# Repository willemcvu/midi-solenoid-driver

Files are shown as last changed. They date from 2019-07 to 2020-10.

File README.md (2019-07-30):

# midi-solenoid-driver
A set of PCBs to drive solenoids using MIDI data, for use in automating musical instruments.

**The boards in this repo will be available for sale shortly on Tindie and/or eBay. If you are interested in buying assembled PCBs or bare PCBs, please send me a message as it would be helpful to know how many might sell. Thanks!**

The system consists of two parts: the solenoid driver board(s), and the USB interface board. The solenoid driver board(s) are daisy-chained via RJ12 ("phone cables"), and at the end of the chain is the USB interface board, which passes MIDI data from the USB port to all the solenoid driver boards (as many driver boards as are needed):

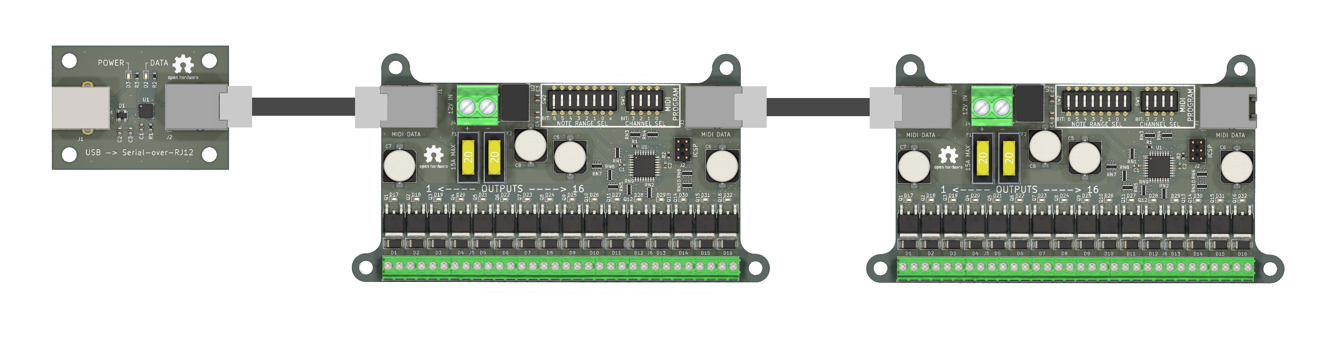
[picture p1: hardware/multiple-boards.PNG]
all boards


In addition to supporting daisy-chaining, the solenoid driver board has several notable features that allow for high usability with limited electronics experience.

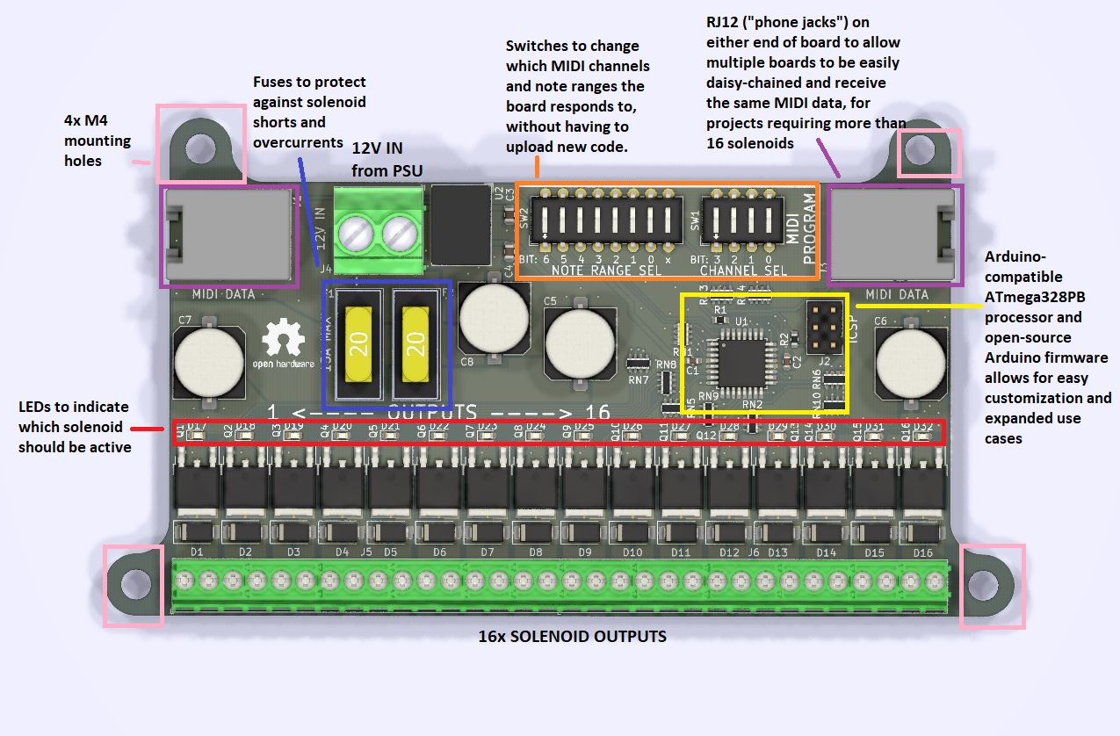
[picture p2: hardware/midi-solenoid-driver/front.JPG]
solenoid board annotated


Currently, MIDI data is fed to the solenoid drivers by a custom USB to serial-over-RJ12 board:

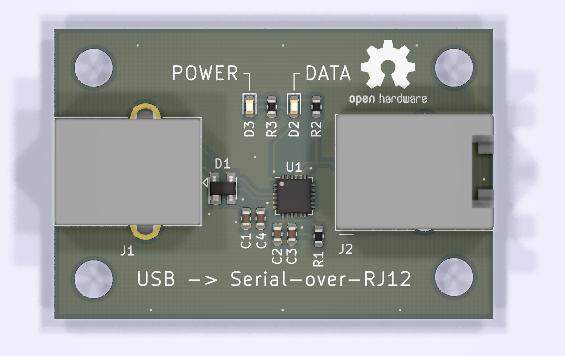
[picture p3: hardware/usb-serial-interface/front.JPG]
usb interface board


In the near future, more RJ12-compatible MIDI interface boards will be designed and released, allowing for more connectivity options. These will likely include:
 - Native plug-and-play USB MIDI (as opposed to the MIDI-over-serial in use right now)
 - Actual MIDI connector
 - Bluetooth adapter
 - AppleMIDI (RTP-MIDI / MIDI-over-network) WiFi interface

Additionally, more driver boards for devices other than solenoids will be designed/released, including a MIDI servo driver.

If you have specific needs for a particular project and need customized hardware, I can probably accomodate. Open an issue or contact me via my blog (https://willemhillier.wordpress.com/)and we'll go from there.

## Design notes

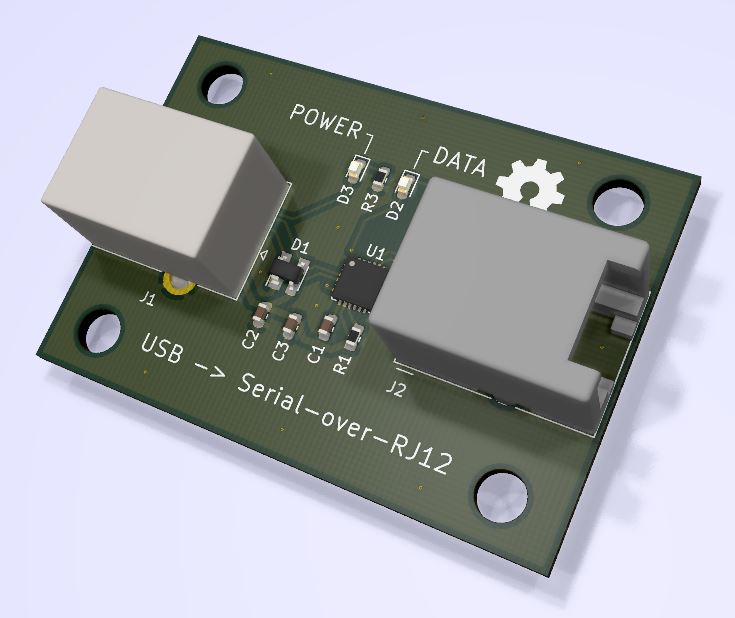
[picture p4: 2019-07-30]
hardware/usb-serial-interface/3d.JPG

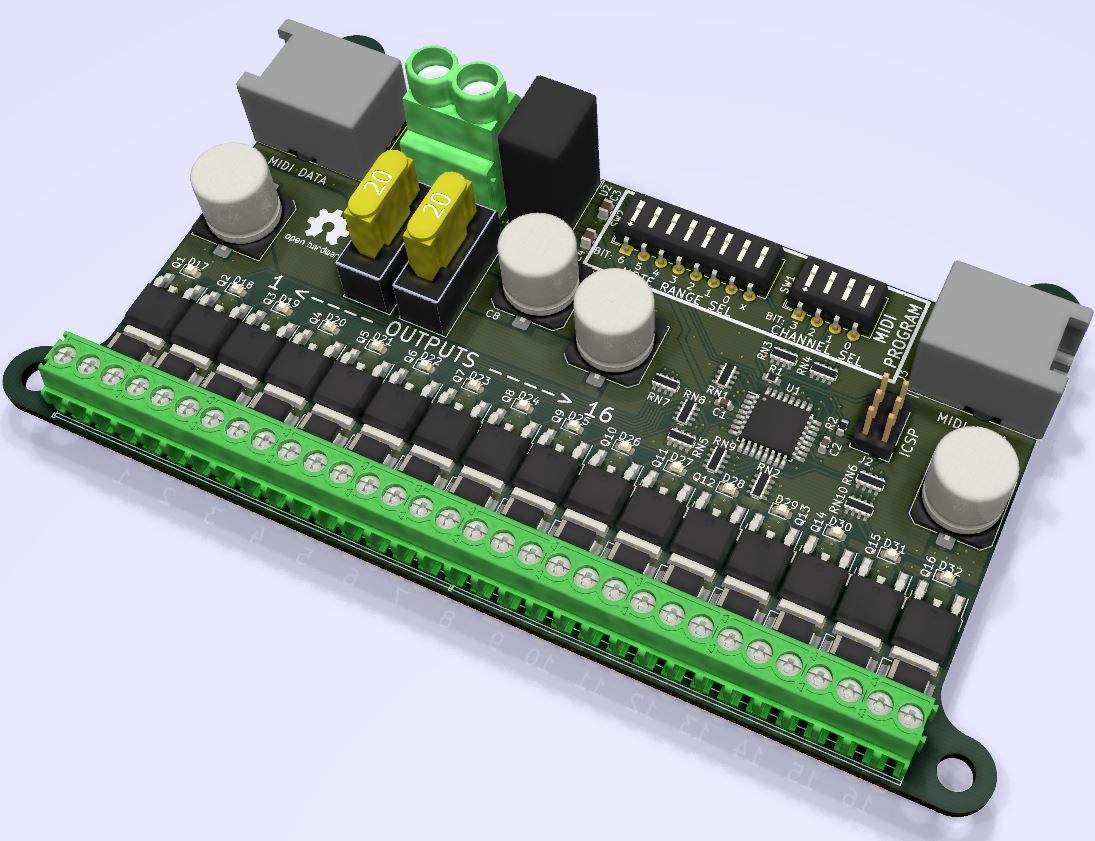
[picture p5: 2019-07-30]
hardware/midi-solenoid-driver/3d.JPG

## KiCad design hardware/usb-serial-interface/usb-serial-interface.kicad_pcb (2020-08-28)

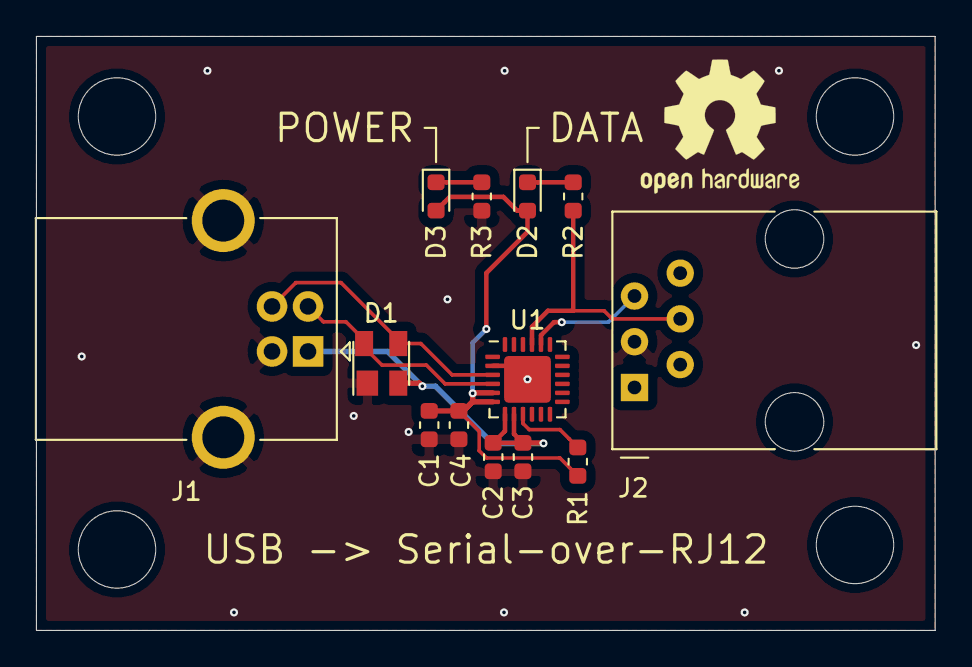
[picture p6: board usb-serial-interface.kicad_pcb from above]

Board: 2 copper layers, 49.9 x 33.0 mm, 13 parts (0 on the bottom side), 10 nets.

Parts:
C1, C2: 4.7u; C_0603_1608Metric
C3, C4: 0.1u; C_0603_1608Metric
D1: SP0503BAHT; SOT-143
D2, D3: LED; LED_0603_1608Metric
J1: USB_B; USB_B_OST_USB-B1HSxx_Horizontal
J2: RJ12; RJ12_Amphenol_54601
R1: 4.7k; R_0603_1608Metric
R2, R3: 1k; R_0603_1608Metric
U1: CP2102N-A01-GQFN24; QFN-24-1EP_4x4mm_P0.5mm_EP2.6x2.6mm

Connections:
+3V3: C1.1, C4.1, D2.2, D3.2, R1.1, U1.5, U1.6
/D+: D1.3, J1.3, U1.3
/D-: D1.4, J1.2, U1.4
/RXD: J2.5, U1.20
/TXD: J2.4, R2.1, U1.21
GND: C1.2, C2.2, C3.2, C4.2, D1.1, J1.4, J1.5, J2.3, R3.1, U1.2, U1.25
unnamed: D2.1, R2.2
unnamed: D3.1, R3.2
unnamed: R1.2, U1.9
VBUS: C2.1, C3.1, D1.2, J1.1, U1.7, U1.8

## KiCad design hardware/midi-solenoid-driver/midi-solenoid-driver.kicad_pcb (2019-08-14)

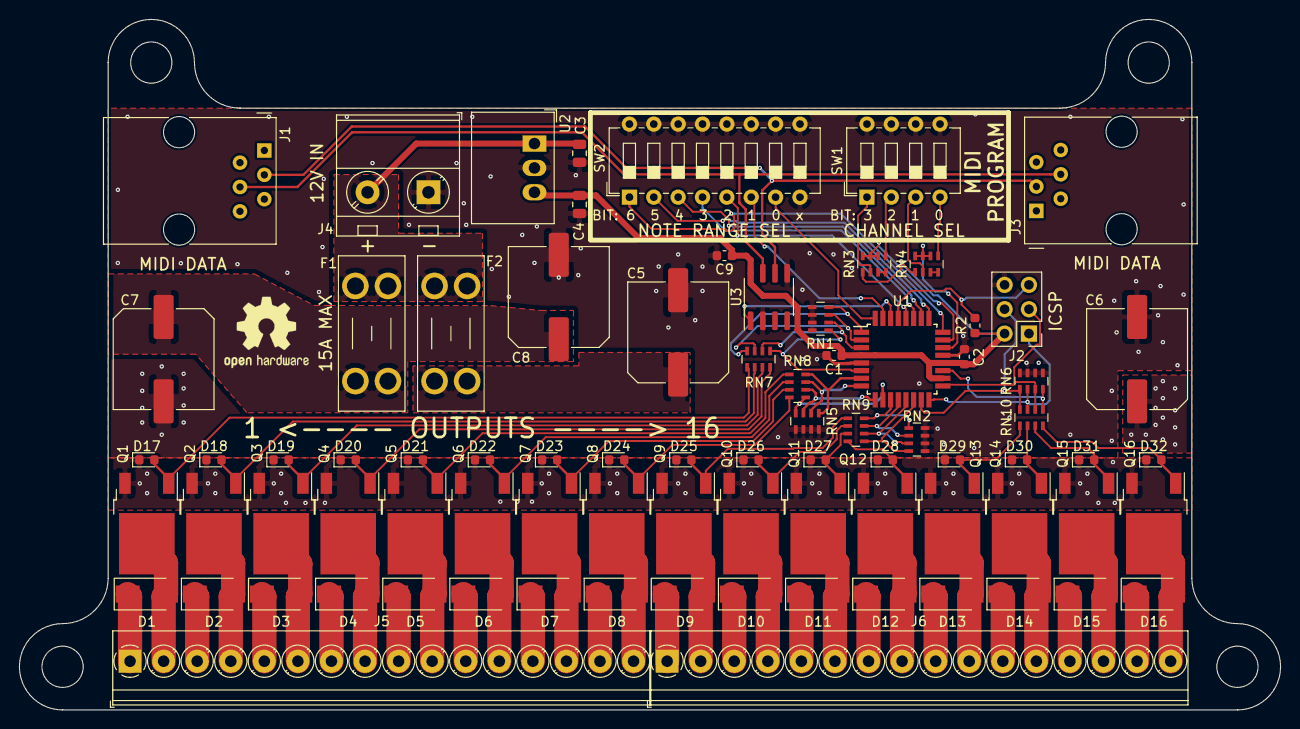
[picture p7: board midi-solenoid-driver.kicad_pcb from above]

Board: 2 copper layers, 131.5 x 72.0 mm, 81 parts (0 on the bottom side), 72 nets.

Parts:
C1, C2, C9: 0.1uF; C_0603_1608Metric
C3, C4: 10uF; C_0805_2012Metric
C5, C6, C7, C8: 470; C_Elec_10x10.2
D1, D2, D3, D4, D5, D6, D7, D8, D9, D10, D11, D12, D13, D14, D15, D16: D_Small; D_SMA
D17, D18, D19, D20, D21, D22, D23, D24, D25, D26, D27, D28, D29, D30, D31, D32: LED_Small; LED_0603_1608Metric
F1, F2: 20A; Fuseholder_Blade_Mini_Keystone_3568
J1: LEFT_DATA; RJ12_Amphenol_54601
J2: Conn_02x03_Odd_Even; PinHeader_2x03_P2.54mm_Vertical
J3: RIGHT_DATA; RJ12_Amphenol_54601
J4: 12V_IN; TerminalBlock_MetzConnect_Type701_RT11L02HGLU_1x02_P6.35mm_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
J5: SOLENOIDS_OUT_1; TerminalBlock_Phoenix_PT-1,5-16-3.5-H_1x16_P3.50mm_Horizont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
J6: SOLENOIDS_OUT_2; TerminalBlock_Phoenix_PT-1,5-16-3.5-H_1x16_P3.50mm_Horizont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
Q1, Q2, Q3, Q4, Q5, Q6, Q7, Q8, Q9, Q10, Q11, Q12, Q13, Q14, Q15, Q16: Q_NMOS_GDS; TO-252-2
R2: 10k; R_0603_1608Metric
RN1, RN2, RN3, RN4, RN5, RN6: 10k; R_Array_Concave_4x0603
RN7, RN8, RN9, RN10: 1k; R_Array_Concave_4x0603
SW1: MIDI_CHANNEl; SW_DIP_SPSTx04_Slide_6.7x11.72mm_W7.62mm_P2.54mm_LowProfile
SW2: SW_DIP_x08; SW_DIP_SPSTx08_Slide_6.7x21.88mm_W7.62mm_P2.54mm_LowProfile
U1: ATmega328PB-AU; TQFP-32_7x7mm_P0.8mm
U2: R-78B5.0-2.0; Converter_DCDC_RECOM_R-78B-2.0_THT
U3: SN75LBC176D; SOIC-8_3.9x4.9mm_P1.27mm

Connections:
+5V: C1.1, C2.1, C4.1, C9.1, J2.2, R2.1, RN3.1, RN4.1, U1.4, U1.18, U1.20, U2.3, U3.8
+12V: C3.1, F1.2, F2.2, J4.2, U2.1
/12V_FUSED1: C7.1, C8.1, D1.1, D2.1, D3.1, D4.1, D5.1, D6.1, D7.1, D8.1, F1.1, J5.1, J5.3, J5.5, J5.7, J5.9, J5.11, J5.13, J5.15
/12V_FUSED2: C5.1, C6.1, D9.1, D10.1, D11.1, D12.1, D13.1, D14.1, D15.1, D16.1, F2.1, J6.1, J6.3, J6.5, J6.7, J6.9, J6.11, J6.13, J6.15
/CTRL1: RN1.4, RN7.8, U1.1
/CTRL2: RN1.3, RN7.7, U1.2
/CTRL3: RN1.2, RN7.6, U1.3
/CTRL4: RN1.1, RN7.5, U1.6
/CTRL5: RN5.1, RN8.8, U1.7
/CTRL6: RN5.2, RN8.7, U1.8
/CTRL7: RN5.3, RN8.6, U1.9
/CTRL8: RN5.4, RN8.5, U1.10
/CTRL9: RN2.1, RN9.8, U1.11
/CTRL10: RN2.2, RN9.7, U1.12
/CTRL11: RN2.3, RN9.6, U1.13
/CTRL12: RN2.4, RN9.5, U1.14
/CTRL13: J2.4, RN6.1, RN10.8, U1.15
/CTRL14: J2.1, RN6.2, RN10.7, U1.16
/CTRL15: J2.3, RN6.3, RN10.6, U1.17
/CTRL16: RN6.4, RN10.5, U1.19
/GATE1: D17.2, Q1.1, RN7.1
/GATE2: D18.2, Q2.1, RN7.2
/GATE3: D19.2, Q3.1, RN7.3
/GATE4: D20.2, Q4.1, RN7.4
/GATE5: D21.2, Q5.1, RN8.1
/GATE6: D22.2, Q6.1, RN8.2
/GATE7: D23.2, Q7.1, RN8.3
/GATE8: D24.2, Q8.1, RN8.4
/GATE9: D25.2, Q9.1, RN9.1
/GATE10: D26.2, Q10.1, RN9.2
/GATE11: D27.2, Q11.1, RN9.3
/GATE12: D28.2, Q12.1, RN9.4
/GATE13: D29.2, Q13.1, RN10.1
/GATE14: D30.2, Q14.1, RN10.2
/GATE15: D31.2, Q15.1, RN10.3
/GATE16: D32.2, Q16.1, RN10.4
/MIDI_CH_BIT0-1: RN3.6, RN3.7, RN3.8, U1.23
/MIDI_CH_BIT2-3: RN4.6, RN4.7, RN4.8, U1.22
/MIDI_IN: U1.30, U3.1
/MIDI_NOTE_BIT0: SW2.1, U1.24
/MIDI_NOTE_BIT1: SW2.2, U1.25
/MIDI_NOTE_BIT2: SW2.3, U1.26
/MIDI_NOTE_BIT3: SW2.4, U1.27
/MIDI_NOTE_BIT4: SW2.5, U1.28
/MIDI_NOTE_BIT5: SW2.6, U1.31
/MIDI_NOTE_BIT6: SW2.7, U1.32
/OUT1: D1.2, J5.2, Q1.2
/OUT2: D2.2, J5.4, Q2.2
/OUT3: D3.2, J5.6, Q3.2
/OUT4: D4.2, J5.8, Q4.2
/OUT5: D5.2, J5.10, Q5.2
/OUT6: D6.2, J5.12, Q6.2
/OUT7: D7.2, J5.14, Q7.2
/OUT8: D8.2, J5.16, Q8.2
/OUT9: D9.2, J6.2, Q9.2
/OUT10: D10.2, J6.4, Q10.2
/OUT11: D11.2, J6.6, Q11.2
/OUT12: D12.2, J6.8, Q12.2
/OUT13: D13.2, J6.10, Q13.2
/OUT14: D14.2, J6.12, Q14.2
/OUT15: D15.2, J6.14, Q15.2
/OUT16: D16.2, J6.16, Q16.2
/RESET: J2.5, R2.2, U1.29
/RS485_A: J1.3, J3.3, U3.6
/RS485_B: J1.4, J3.4, U3.7
GND: C1.2, C2.2, C3.2, C4.2, C5.2, C6.2, C7.2, C8.2, C9.2, D17.1, D18.1, D19.1, D20.1, D21.1, D22.1, D23.1, D24.1, D25.1, D26.1, D27.1, D28.1, D29.1, D30.1, D31.1, D32.1, J2.6, J4.1, Q1.3, Q2.3, Q3.3, Q4.3, Q5.3, Q6.3, Q7.3, Q8.3, Q9.3, Q10.3, Q11.3, Q12.3, Q13.3, Q14.3, Q15.3, Q16.3, RN1.5, RN1.6, RN1.7, RN1.8, RN2.5, RN2.6, RN2.7, RN2.8, RN5.5, RN5.6, RN5.7, RN5.8, RN6.5, RN6.6, RN6.7, RN6.8, SW1.5, SW1.6, SW1.7, SW1.8, SW2.8, SW2.9, SW2.10, SW2.11, SW2.12, SW2.13, SW2.14, SW2.15, SW2.16, U1.5, U1.21, U2.2, U3.2, U3.5
unnamed: RN3.2, SW1.1
unnamed: RN3.3, RN3.4
unnamed: RN3.5, SW1.2
unnamed: RN4.2, SW1.3
unnamed: RN4.3, RN4.4
unnamed: RN4.5, SW1.4

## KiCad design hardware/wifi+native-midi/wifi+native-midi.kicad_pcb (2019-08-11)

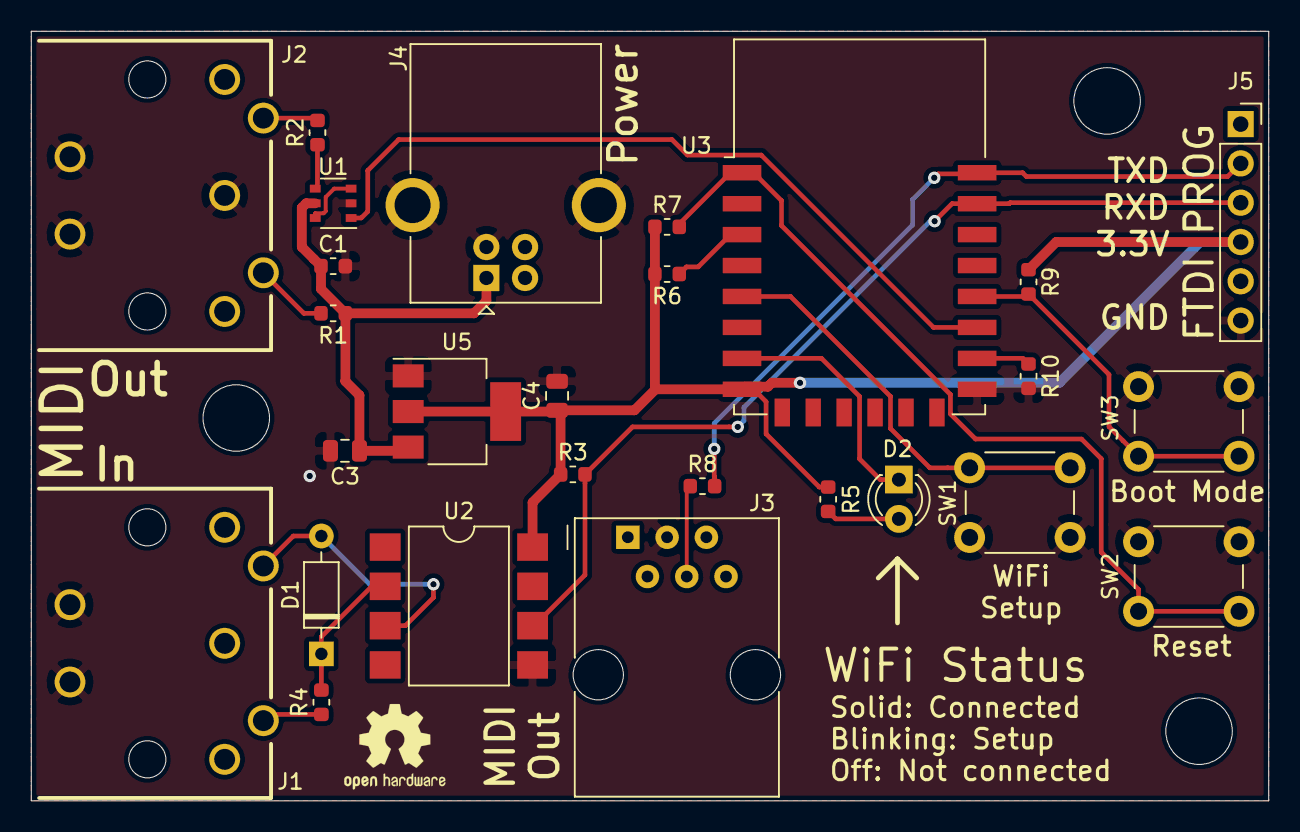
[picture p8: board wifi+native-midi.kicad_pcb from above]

Board: 2 copper layers, 80.0 x 49.8 mm, 27 parts (0 on the bottom side), 21 nets.

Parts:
C1: 0.1u; C_0603_1608Metric
C3, C4: 10u; C_0805_2012Metric
D1: 1N914; D_DO-35_SOD27_P7.62mm_Horizontal
D2: LED; LED_D3.0mm
J1: MIDI_RX; 57PC5F_5_DIN_MIDI_GENERIC
J2: MIDI_TX; 57PC5F_5_DIN_MIDI_GENERIC
J3: 6P6C; RJ12_Amphenol_54601
J4: USB_B; USB_B_OST_USB-B1HSxx_Horizontal
J5: FTDI; PinSocket_1x06_P2.54mm_Vertical
R1, R2: 220; R_0603_1608Metric
R3: 470; R_0603_1608Metric
R4, R5: 1k; R_0603_1608Metric
R6, R7, R9, R10: 10k; R_0603_1608Metric
R8: 330; R_0603_1608Metric
SW1: WIFI_CONFIG; SW_PUSH_6mm_H9.5mm
SW2: RESET; SW_PUSH_6mm_H9.5mm
SW3: BOOT_MODE; SW_PUSH_6mm_H9.5mm
U1: 74HC2G04; TSOP-6_1.65x3.05mm_P0.95mm
U2: 6N138; SMDIP-8_W9.53mm
U3: ESP-12F; ESP-12E
U5: AZ1117-3.3; SOT-223-3_TabPin2

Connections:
+3V3: C4.1, J5.4, R3.1, R5.1, R6.2, R7.1, R9.1, U2.8, U3.8, U5.2
+5V: C1.1, C3.1, J4.1, R1.1, U1.5, U5.3
/GPIO0: R9.2, SW3.2, U3.18
/MIDI_IN: J5.3, R3.2, U2.6, U3.21
/MIDI_OUT: U1.1, U3.17
/RJ12_MIDI_OUT: J5.2, R8.2, U3.22
/RST: R7.2, SW2.2, U3.1
/WIFI_CONFIG: SW1.1, U3.5
/WIFI_STATUS: D2.1, U3.7
GND: C1.2, C3.2, C4.2, J1.GND, J2.2, J2.GND, J3.3, J4.4, J4.5, J5.6, R10.2, SW1.2, SW2.1, SW3.1, U1.2, U2.5, U3.15, U5.1
unnamed: D1.1, R4.2, U2.2
unnamed: D1.2, J1.5, U2.3
unnamed: D2.2, R5.2
unnamed: J1.4, R4.1
unnamed: J2.4, R1.2
unnamed: J2.5, R2.2
unnamed: J3.4, R8.1
unnamed: R2.1, U1.4
unnamed: R6.1, U3.3
unnamed: R10.1, U3.16
unnamed: U1.3, U1.6

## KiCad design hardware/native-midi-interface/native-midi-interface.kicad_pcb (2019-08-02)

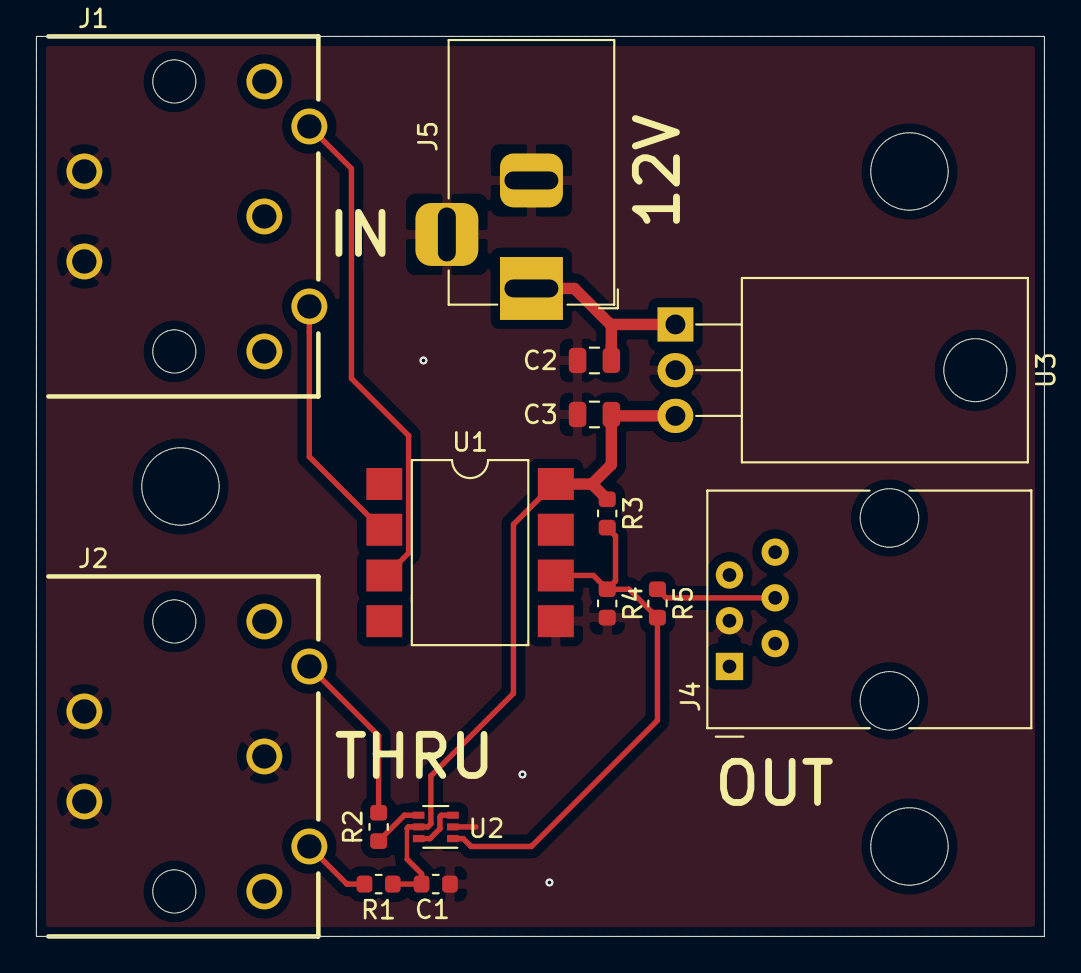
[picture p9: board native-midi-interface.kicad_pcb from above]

Board: 2 copper layers, 56.0 x 50.0 mm, 15 parts (0 on the bottom side), 11 nets.

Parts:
C1: 1u; C_0603_1608Metric
C2, C3: 10u; C_0805_2012Metric
J1: MIDI_RX; 57PC5F_5_DIN_MIDI_GENERIC
J2: MIDI_PASSTHROUGH; 57PC5F_5_DIN_MIDI_GENERIC
J4: 6P6C; RJ12_Amphenol_54601
J5: BARREL_JACK_12V; BarrelJack_Horizontal
R1, R2: 220; R_0603_1608Metric
R3: 470; R_0603_1608Metric
R4: 1k; R_0603_1608Metric
R5: 330; R_0603_1608Metric
U1: 6N138; SMDIP-8_W9.53mm
U2: 74HC2G04; SOT-363_SC-70-6
U3: L7805; TO-220-3_Horizontal_TabDown

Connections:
+5V: C1.1, C3.1, R1.1, R3.1, U1.8, U2.5, U3.3
+12V: C2.1, J5.1, U3.1
/MIDI_UART: R3.2, R4.1, R5.2, U1.6, U2.1
GND: C1.2, C2.2, C3.2, J1.GND, J2.2, J2.GND, J4.3, J5.2, J5.3, R4.2, U1.5, U2.2, U3.2
unnamed: J1.4, U1.2
unnamed: J1.5, U1.3
unnamed: J2.4, R1.2
unnamed: J2.5, R2.2
unnamed: J4.4, R5.1
unnamed: R2.1, U2.4
unnamed: U2.3, U2.6

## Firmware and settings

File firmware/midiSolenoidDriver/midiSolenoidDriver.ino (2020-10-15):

//Firmware for the MIDI solenoid driver board: https://github.com/willemcvu/midi-solenoid-driver
//Author: Willem Hillier, with MIDI decoding code taken from: https://forum.arduino.cc/index.php?topic=22447.0

//Configuration constants
#define SETUP_TEST_DELAY 100

//Pin mappings for big dip switch input, used for selecting the MIDI note number of the lowest note the board responds to
byte MIDI_NOTE_BIT[] =  {15, 16, 17, 18, 19, 1, 2};

// Digital output pin mappings in sequential order ("OUTPUTS 1-16")
byte pinNumbers[] = {3, 4, 23, 24, 20, 21, 5, 6, 7, 8, 9, 10, 11, 12, 13, 25};

// Global vars
byte MIDI_CHANNEL = 0;
byte LOWEST_MIDI_NOTE = 0;
byte incomingByte;
byte byteNumber = 0;
byte note;
byte velocity;
int action = 2;

boolean readSmallDip(int bitNo) {
  boolean bit0 = false;
  boolean bit1 = false;
  boolean bit2 = false;
  boolean bit3 = false;

  int adc_bit01_val = analogRead(A0);
  int adc_bit23_val = analogRead(A7);

  if (adc_bit01_val > 750) {
    bit0 = false;
    bit1 = false;
  } else if ((adc_bit01_val > 550) and (adc_bit01_val <= 750)) {
    bit0 = false;
    bit1 = true;
  } else if ((adc_bit01_val > 480) and (adc_bit01_val <= 550)) {
    bit0 = true;
    bit1 = false;
  } else if ((adc_bit01_val <= 480)) {
    bit0 = true;
    bit1 = true;
  }

  if (adc_bit23_val > 750) {
    bit2 = false;
    bit3 = false;
  } else if ((adc_bit23_val > 550) and (adc_bit23_val < 750)) {
    bit2 = false;
    bit3 = true;
  } else if ((adc_bit23_val > 480) and (adc_bit23_val <= 550)) {
    bit2 = true;
    bit3 = false;
  } else if ((adc_bit23_val <= 480)) {
    bit2 = true;
    bit3 = true;
  }

  if (bitNo == 0) {
    return bit0;
  } else if (bitNo == 1) {
    return bit1;
  } else if (bitNo == 2) {
    return bit2;
  } else if (bitNo == 3) {
    return bit3;
  } else {
    return false;
  }
}

void TestDipSwitches() {
  while (1 == 1) {

    //Set first 7 outputs to the state of the large dip switch
    digitalWrite(pinNumbers[0], ! digitalRead(MIDI_NOTE_BIT[6]));
    digitalWrite(pinNumbers[1], ! digitalRead(MIDI_NOTE_BIT[5]));
    digitalWrite(pinNumbers[2], ! digitalRead(MIDI_NOTE_BIT[4]));
    digitalWrite(pinNumbers[3], ! digitalRead(MIDI_NOTE_BIT[3]));
    digitalWrite(pinNumbers[4], ! digitalRead(MIDI_NOTE_BIT[2]));
    digitalWrite(pinNumbers[5], ! digitalRead(MIDI_NOTE_BIT[1]));
    digitalWrite(pinNumbers[6], ! digitalRead(MIDI_NOTE_BIT[0]));

    // Set first four outputs to the state of the small dip switch
    digitalWrite(pinNumbers[7], readSmallDip(0));
    digitalWrite(pinNumbers[8], readSmallDip(1));
    digitalWrite(pinNumbers[9], readSmallDip(2));
    digitalWrite(pinNumbers[10], readSmallDip(3));
  }
}

void setup() {
  //Set output pins mode
  for (int n = 0; n < 16; n++) {
    pinMode(pinNumbers[n], OUTPUT);
  }

  //DIP switch input mode
  for (int n = 0; n < 7; n++) {
    pinMode(MIDI_NOTE_BIT[n], INPUT_PULLUP);
  }

  // test outputs
  for (int n = 0; n < 16; n++) {
    digitalWrite(pinNumbers[n], HIGH);
    delay(SETUP_TEST_DELAY);
    digitalWrite(pinNumbers[n], LOW);
  }

  // test DIP switches
  //TestDipSwitches();
  //The above function is an infinite while-loop. Reflash this firmware with the above line uncommented, and the status of the ouputs will mirror the status of the DIP switches.
  //Useful for testing outputs and DIP switches.

  //read midi channel to respond to, zero-indexed (!! most midi software is 1-indexed !!)
  if (readSmallDip(3)) MIDI_CHANNEL = MIDI_CHANNEL + 1;
  if (readSmallDip(2)) MIDI_CHANNEL = MIDI_CHANNEL + 2;
  if (readSmallDip(1)) MIDI_CHANNEL = MIDI_CHANNEL + 4;
  if (readSmallDip(0)) MIDI_CHANNEL = MIDI_CHANNEL + 8;

  //read lowest midi note to respond to
  if (!digitalRead(MIDI_NOTE_BIT[0])) LOWEST_MIDI_NOTE = LOWEST_MIDI_NOTE + 1;
  if (!digitalRead(MIDI_NOTE_BIT[1])) LOWEST_MIDI_NOTE = LOWEST_MIDI_NOTE + 2;
  if (!digitalRead(MIDI_NOTE_BIT[2])) LOWEST_MIDI_NOTE = LOWEST_MIDI_NOTE + 4;
  if (!digitalRead(MIDI_NOTE_BIT[3])) LOWEST_MIDI_NOTE = LOWEST_MIDI_NOTE + 8;
  if (!digitalRead(MIDI_NOTE_BIT[4])) LOWEST_MIDI_NOTE = LOWEST_MIDI_NOTE + 16;
  if (!digitalRead(MIDI_NOTE_BIT[5])) LOWEST_MIDI_NOTE = LOWEST_MIDI_NOTE + 32;
  if (!digitalRead(MIDI_NOTE_BIT[6])) LOWEST_MIDI_NOTE = LOWEST_MIDI_NOTE + 64;

  //begin serial receive, no transmit
  Serial.begin(38400);
  //Disable hardware UART transmit
  UCSR0B &= ~bit (TXEN0);
}

//loop: wait for serial data, and interpret the message
void loop () {
  if (Serial.available() > 0) {
    //digitalWrite(pinNumbers[15],HIGH);
    //delay(1);
    //digitalWrite(pinNumbers[15],LOW);
    // read the incoming byte:
    incomingByte = Serial.read();

    // wait for as status-byte, channel 1, note on or off
    if (incomingByte == 144 + MIDI_CHANNEL) { // note on message starting starting
      //digitalWrite(pinNumbers[14],HIGH);
      //delay(1);
      //digitalWrite(pinNumbers[14],LOW);
      action = 1;
      byteNumber = 1;
    } else if (incomingByte == 128 + MIDI_CHANNEL) { // note off message starting
      action = 0;
      byteNumber = 1;
    } else if (incomingByte == 208) { // aftertouch message starting
      //not implemented yet
    } else if (incomingByte == 160) { // polypressure message starting
      //not implemented yet
    } else if ( (action == 0) && (byteNumber == 1) ) { // if we received a "note off", we wait for which note (databyte)
      note = incomingByte;
      playNote(note, 0);
      note = 0;
      velocity = 0;
      action = 2;
      byteNumber = 0;
    } else if ( (action == 1) && (byteNumber == 1) ) { // if we received a "note on", we wait for the note (databyte)
      note = incomingByte;
      byteNumber = 2;
    } else if ( (action == 1) && (byteNumber == 2) ) { // ...and then the velocity
      velocity = incomingByte;
      playNote(note, velocity);
      note = 0;
      velocity = 0;
      action = 0;
      byteNumber = 0;
    } else {
    }
  }
}

void playNote(byte note, byte velocity) {
  //digitalWrite(pinNumbers[13],HIGH);
  //delay(1);
  //digitalWrite(pinNumbers[13],LOW);
  int value = LOW;
  if (velocity > 0) {
    value = HIGH;
  } else {
    value = LOW;
  }

  //play note if it's in the correct range
  if ((note >= LOWEST_MIDI_NOTE) and (note < LOWEST_MIDI_NOTE + 16)) {
    digitalWrite(pinNumbers[note - LOWEST_MIDI_NOTE], value);
    //digitalWrite(pinNumbers[12],value);
  }
}

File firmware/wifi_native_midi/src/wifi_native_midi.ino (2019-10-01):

#include <Arduino.h>
#include <WiFiManager.h>

#include <ESP8266WiFi.h>
#include <WiFiClient.h>
#include <WiFiUdp.h>

#include "MIDI.h" // dependency: https://github.com/FortySevenEffects/arduino_midi_library 
#include "AppleMidi.h"

unsigned long t0 = millis();
bool isConnected = false;

APPLEMIDI_CREATE_INSTANCE(WiFiUDP, AppleMIDI); // see definition in AppleMidi_Defs.h

WiFiManager wifiManager;


// Created and binds the MIDI interface to the default hardware Serial port
MIDI_CREATE_INSTANCE(HardwareSerial,Serial1,nativeMidi);
//MIDI_CREATE_CUSTOM_INSTANCE(HardwareSerial,Serial,rj12Midi,rj12MidiSettings);

// -----------------------------------------------------------------------------
//
// -----------------------------------------------------------------------------
//for LED status

#include <Ticker.h>
Ticker ticker;

void tick()
{
  //toggle state
  int state = digitalRead(BUILTIN_LED);  // get the current state of GPIO1 pin
  digitalWrite(BUILTIN_LED, !state);     // set pin to the opposite state
}

//gets called when WiFiManager enters configuration mode
void configModeCallback (WiFiManager *myWiFiManager) {
  Serial.println("Entered config mode");
  Serial.println(WiFi.softAPIP());
  //if you used auto generated SSID, print it
  Serial.println(myWiFiManager->getConfigPortalSSID());
  //entered config mode, make led toggle faster
  ticker.attach(0.2, tick);
}

// -----------------------------------------------------------------------------
//
// -----------------------------------------------------------------------------

void setup() {
  Serial.begin(38400);
  
  //set led pin as output
  pinMode(BUILTIN_LED, OUTPUT);
  // start ticker with 0.5 because we start in AP mode and try to connect
  ticker.attach(0.6, tick);

  //WiFiManager
  //Local intialization. Once its business is done, there is no need to keep it around
  WiFiManager wifiManager;
  //reset settings - for testing
  //wifiManager.resetSettings();

  //set callback that gets called when connecting to previous WiFi fails, and enters Access Point mode
  wifiManager.setAPCallback(configModeCallback);

  //fetches ssid and pass and tries to connect
  //if it does not connect it starts an access point with the specified name
  //here  "AutoConnectAP"
  //and goes into a blocking loop awaiting configuration
  if (!wifiManager.autoConnect()) {
    //reset and try again, or maybe put it to deep sleep
    ESP.reset();
    delay(1000);
  }
  
  //if you get here you have connected to the WiFi
  Serial.println("connected...yeey :)");
  ticker.detach();
  //keep LED on
  digitalWrite(BUILTIN_LED, LOW);

    // Create a session and wait for a remote host to connect to us
  AppleMIDI.begin("test");

  AppleMIDI.OnConnected(OnAppleMidiConnected);
  AppleMIDI.OnDisconnected(OnAppleMidiDisconnected);

  AppleMIDI.OnReceiveNoteOn(OnAppleMidiNoteOn);
  AppleMIDI.OnReceiveNoteOff(OnAppleMidiNoteOff);

  pinMode(13,OUTPUT);
  digitalWrite(13,HIGH);
}
  
void loop()
{
  // Listen to incoming notes
  AppleMIDI.read();

  // Read incoming messages
  nativeMidi.read();
  //rj12Midi.read();
}

// ====================================================================================
// Event handlers for incoming MIDI messages
// ====================================================================================

// -----------------------------------------------------------------------------
// rtpMIDI session. Device connected
// -----------------------------------------------------------------------------
void OnAppleMidiConnected(uint32_t ssrc, char* name) {
  isConnected = true;
#ifdef SERIAL_DEBUG_ON
  Serial.print(F("Connected to session "));
  Serial.println(name);
#endif  
}

// -----------------------------------------------------------------------------
// rtpMIDI session. Device disconnected
// -----------------------------------------------------------------------------
void OnAppleMidiDisconnected(uint32_t ssrc) {
  isConnected = false;
#ifdef SERIAL_DEBUG_ON
  Serial.println(F("Disconnected"));
#endif
}

// -----------------------------------------------------------------------------
//
// -----------------------------------------------------------------------------
static void OnAppleMidiNoteOn(byte channel, byte note, byte velocity) {
#ifdef SERIAL_DEBUG_ON
  Serial.println(F("received noteOn via rtp, sending via serial MIDI"));
#endif
  nativeMidi.sendNoteOn(note, velocity, channel);
  //rj12Midi.sendNoteOn(note, velocity, channel);
  Serial.write(144+channel);
  Serial.write(note);
  Serial.write(velocity);
  digitalWrite(13,LOW);
}

// -----------------------------------------------------------------------------
//
// -----------------------------------------------------------------------------
static void OnAppleMidiNoteOff(byte channel, byte note, byte velocity) {
#ifdef SERIAL_DEBUG_ON
  Serial.println(F("received noteOff via rtp, sending via serial MIDI"));
#endif
  nativeMidi.sendNoteOff(note, velocity, channel);
  //rj12Midi.sendNoteOff(note, velocity, channel);
  Serial.write(128+channel);
  Serial.write(note);
  Serial.write(velocity);
  digitalWrite(13,HIGH);
  
}
//Hello, this is Haley Warren commenting for EE106

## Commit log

2019-07-27 Schematic done
    [midi-solenoid-driver.kicad_pcb, midi-solenoid-driver.sch]
2019-07-28 mostly finished PCB layout
    Done w/ all but reference designators and silkscreen cleanup
    [midi-solenoid-driver.kicad_pcb, midi-solenoid-driver.sch]
2019-07-28 PCB mostly done.
    [midi-solenoid-driver.kicad_pcb]
2019-07-29 USB interface schematic done
    [midi-solenoid-driver.kicad_pcb, solenoid-driver-hub.kicad_pcb, solenoid-driver-hub.sch]
2019-07-29 USB to serial board done
    - Finished laying out
    - Added RX line to RJ12 for potential future use
    - Made gerbers
    [solenoid-driver-hub.kicad_pcb, solenoid-driver-hub.sch]
2019-07-29 Added OSHW logo to driver board
    - Added logo
    - Made new gerbers
    [midi-solenoid-driver.kicad_pcb, solenoid-driver-hub.kicad_pcb]
2019-07-29 Removed thermal reliefs on high-current pins + made new gerbers
    [midi-solenoid-driver.kicad_pcb]
2019-07-30 Added solenoid driver board renders + diagram
2019-07-30 Made multi-board layout pic
    [solenoid-driver-hub.kicad_pcb]
2019-07-30 Added more info about USB interface board
2019-07-30 Added pics of USB interface board
2019-07-30 Updated USB interface terminology
    [usb-serial-interface.kicad_pcb, usb-serial-interface.sch]
2019-08-02 Made native midi interface
    TODO: Update readme to reflect the existance of this board
    [native-midi-interface.kicad_pcb, native-midi-interface.sch]
2019-08-11 Made v2 of serial interface + panelized
    [usb-serial-interface.kicad_pcb, usb-serial-interface.sch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]
2019-08-11 Made v1.1 of driver board + gerbers
    - Added thermal relief to difficult-to-solder pads
    - Updated silkscreen
    [midi-solenoid-driver-B_Cu.gbr, midi-solenoid-driver-B_Mask.gbr, midi-solenoid-driver-B_Paste.gbr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]
2019-08-11 Fixed gerber locations
    [midi-solenoid-driver-B_Cu.gbr, midi-solenoid-driver-B_Mask.gbr, midi-solenoid-driver-B_Paste.gbr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]
2019-08-11 made schematic for wifi-native-midi
    [wifi+native-midi.kicad_pcb, wifi+native-midi.sch]
2019-08-11 Shipping wifi+native-midi
    [wifi+native-midi.kicad_pcb, wifi+native-midi.sch, wifi+native-midi_panelized.kicad_pcb]
2019-08-12 Update wifi+native-midi_panelized.kicad_pcb
    Updated panelized version
    [wifi+native-midi_panelized.kicad_pcb]
2019-08-14 AddedRS485 transceiver, need to ship new rev
    [midi-solenoid-driver.kicad_pcb, midi-solenoid-driver.sch]
2019-08-16 Lowest MIDI note selection via DIP switchesa now works properly
2019-08-21 Channel assignment via DIP switches now works properly
2019-08-26 New USB to serial board image
    [usb-serial-interface.kicad_pcb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]
2019-09-16 Initial commit of wifi-native-midi firmware. Not working.
    [wifi_native_midi.ino]
2019-10-01 Test commit for EE106
    [usb-serial-interface.kicad_pcb]
2020-08-28 new usb serial gerbers
    [usb-serial-interface-B_Cu.gbr, usb-serial-interface-B_Mask.gbr, usb-serial-interface-B_Paste.gbr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]
2020-10-02 Fix potential array index out of bounds error
    [midiSolenoidDriver.ino]
2020-10-02 Fix note 0 bug
    When the Note Range Selection dip switches were set to 0, it was impossible to activate the first mosfet, (Q1 / note 0 in this configuration)
    [midiSolenoidDriver.ino]
